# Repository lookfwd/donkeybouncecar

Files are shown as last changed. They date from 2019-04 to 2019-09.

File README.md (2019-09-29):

# Donkey Bounce Car
The Donkey Bounce Car is the [Donkey Car](https://www.donkeycar.com/) + super fancy extra hardware and software.

## Videos

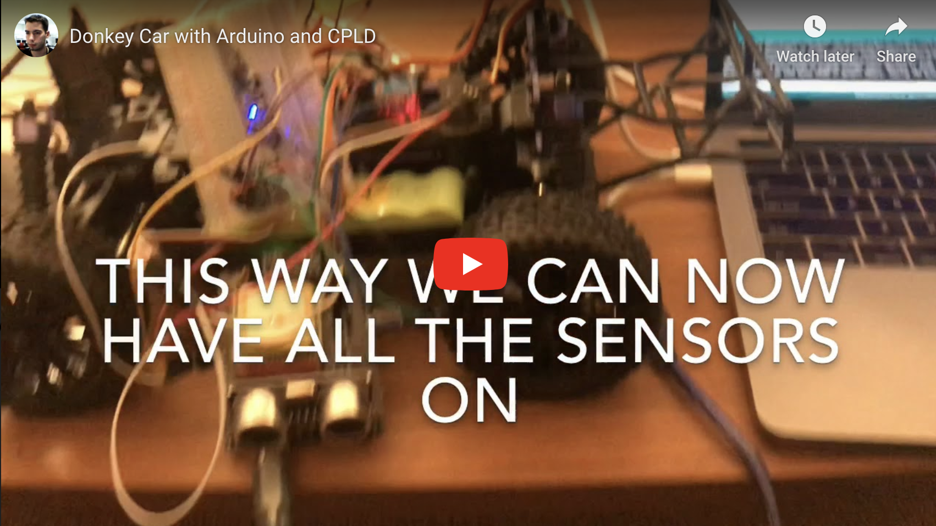
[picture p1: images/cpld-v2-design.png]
Watch the video (https://www.youtube.com/watch?v=cjI4cC8FCgs)


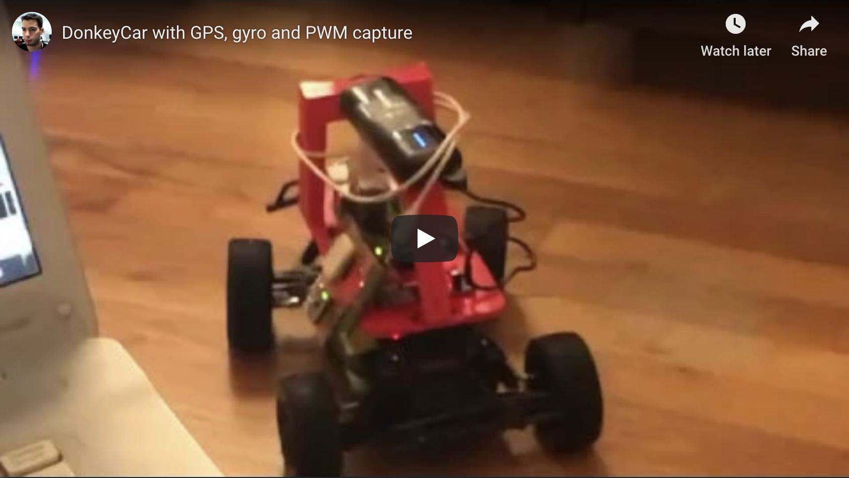
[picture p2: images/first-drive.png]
Watch the video (https://www.youtube.com/watch?v=y7wChCVcuVY)


## Donkey Bounce Shield II

### Goal
The second version of the Donkey Bounce Shield, uses a CPLD to accuratelly measure Servo signals from the Remote Control (RC). It creates PWM signals that drive both steering and throttle and by default it mirrors the signals of the RC. Alternatively, Arduino's serial port can override RC settings and drive the car. It also now supports various types of GPSs and both 6-axis and 9-axis absolute position sensors.

* You can find the PCB [here](https://oshpark.com/shared_projects/81d3538F).
* You can find the CPLD design and JTAG files [here](shield/servo-reader-xc2c64a).
* You can find the latest Arduino Sketch [here](shield/gps-gyro-pwm-sketch).
* You can find the updated ServoTimer1 library [here](shield/ServoTimer1).

The schematic

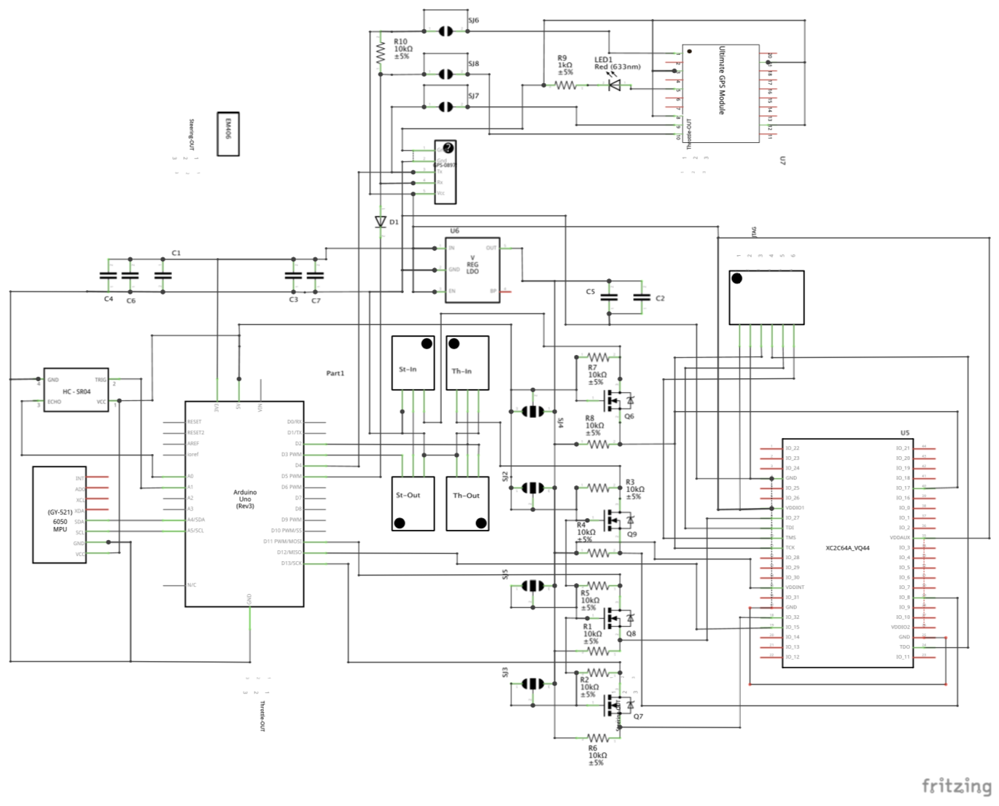
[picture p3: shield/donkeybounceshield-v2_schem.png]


or - 

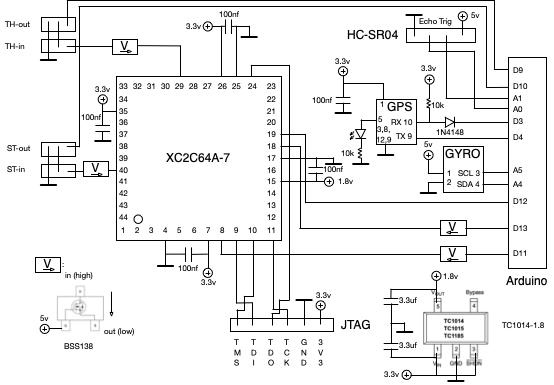
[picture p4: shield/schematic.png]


The Shield

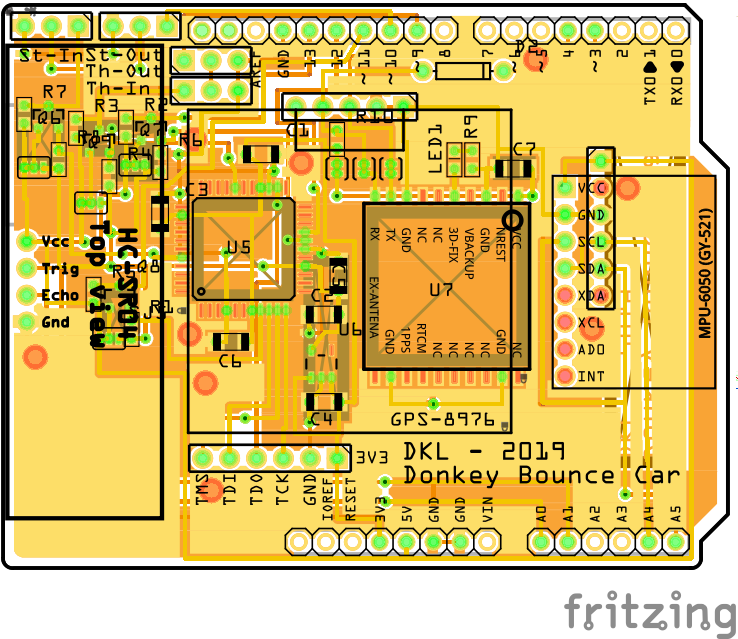
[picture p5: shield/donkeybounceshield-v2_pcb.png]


### Rationale

As soon as I started using the first version of the Donkey Bounce Shield, several limitations became aparent:

1. Servo pulse width measurements were highly inaccurate. Even after using interrupts and other techniques the accuracy was bad.
2. I would have to manually unplug the Remote Control signals in order to create control signals from Arduino.
3. When, after several modifications I was able to have arduino as man-in-the-middle, between the RC and the motors, Donkey Car was making flaky small moves as inaccurate measurements where propagated to the PWM controller.

The reason for inaccurate measurements was the sensitivity on interrupts. More specifically the `cli` command stops interrupts and it's used very often. For example, it's used by the `micros()` Arduino command and it's also very heavily used by the SoftwareSerial module. We need that module in order to read GPS signals.

Bottom line; In order to accurately read PWM signals you need to measure latencies with microsecond-level precision and an Arduino can't do that when it's as busy as it is in our case. I offloaded this work to [custom hardware and more specifically an XC2C64A Xilinx CPLD](servo-reader-xc2c64a).

### References

* [Use the Matrix Glitcher as a Coolrunner II XC2C64A development board](http://blog.dimitrioskouzisloukas.com/2019/08/use-matrix-glitcher-as-coolrunner-ii.html)
* [XC2C64A CoolRunner-II CPLD Datasheet](https://www.xilinx.com/support/documentation/data_sheets/ds311.pdf)
* [Datasheet of GPS smart antenna module, LS20030~3](https://cdn.sparkfun.com/datasheets/GPS/LS20030~3_datasheet_v1.3.pdf)
* [FGPMMOPA6H GPS Standalone Module Data Sheet](https://cdn-shop.adafruit.com/datasheets/GlobalTop-FGPMMOPA6H-Datasheet-V0A.pdf)
* [Adafruit Ultimate GPS v3 Schematic](https://learn.adafruit.com/adafruit-ultimate-gps/downloads)
* [Dangerous Prototypes XC2C64A cpld breakout Schematic](http://dangerousprototypes.com/docs/File:Cct-XC2C_64a-cpld-breakout-v1a.png)
* [TC1014/TC1015/TC1185 Voltage Regulators](http://ww1.microchip.com/downloads/en/devicedoc/21335e.pdf)
* [Logic Level Bidirectional Adaptor Schematic](https://cdn.sparkfun.com/datasheets/BreakoutBoards/Logic_Level_Bidirectional.pdf)
* [5V Tolerance Techniques for CoolRunner-II Devices](https://www.xilinx.com/support/documentation/application_notes/xapp429.pdf)
* [BSS138 N-Channel Logic Level Enhancement Mode Field Effect Transistor](https://cdn.sparkfun.com/datasheets/BreakoutBoards/BSS138.pdf)
* [Adafruit BNO055 Absolute Orientation Sensor](https://learn.adafruit.com/adafruit-bno055-absolute-orientation-sensor?view=all)

## Donkey Bounce Shield I

### What

A shield that adds a GPS, a gyro, PWM monitors and a distance sensor

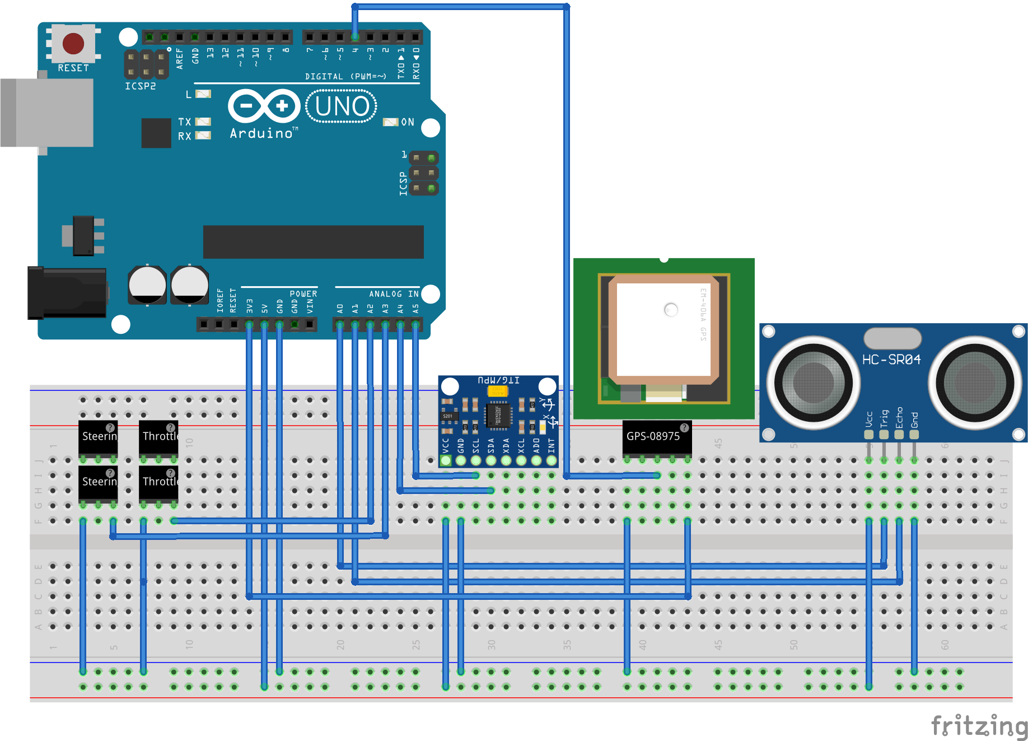
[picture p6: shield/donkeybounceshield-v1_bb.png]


The schematic

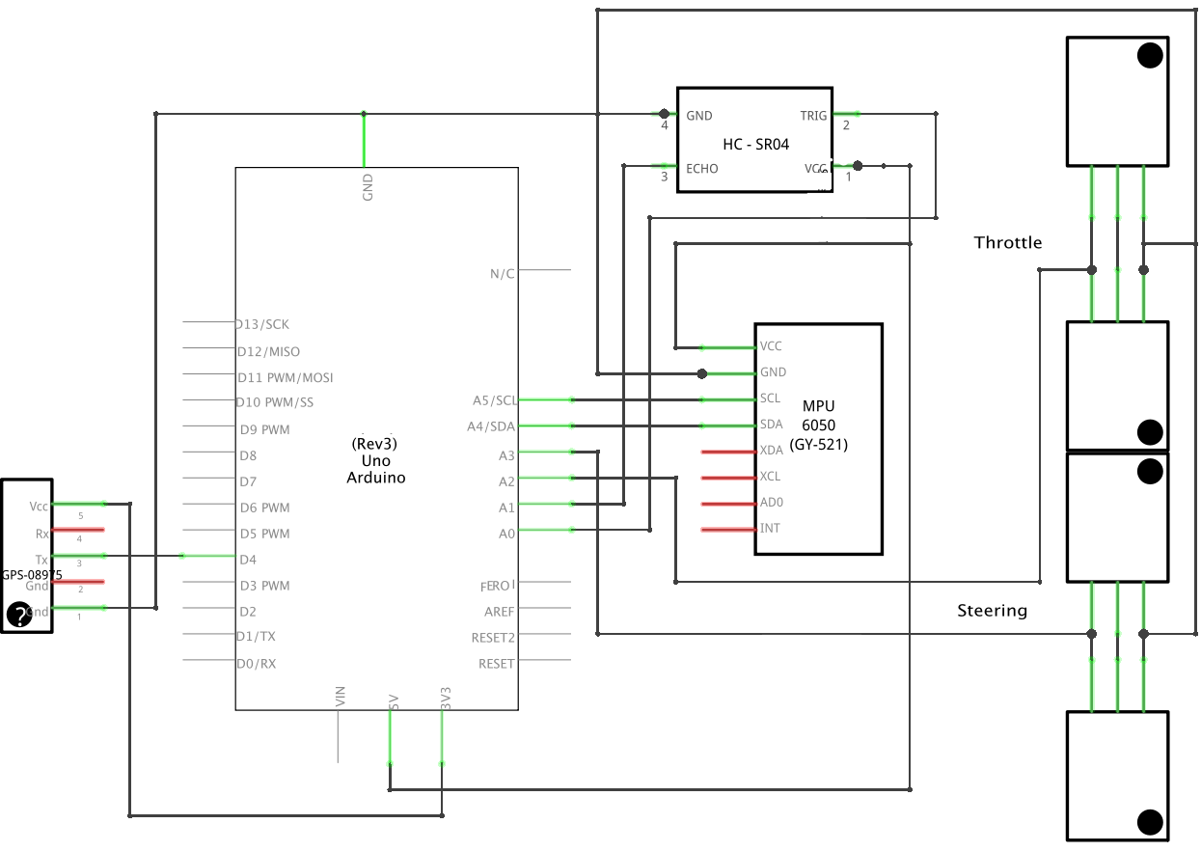
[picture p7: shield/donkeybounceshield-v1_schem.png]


The Shield

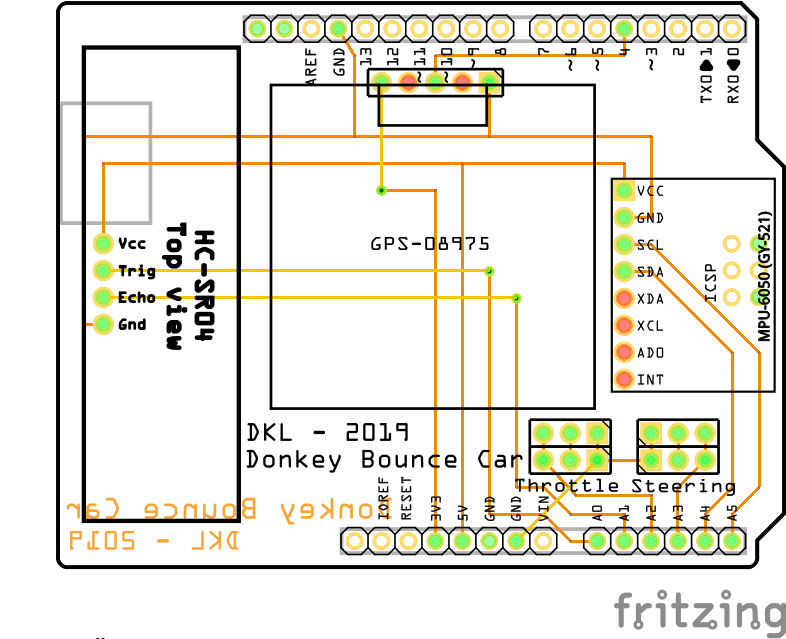
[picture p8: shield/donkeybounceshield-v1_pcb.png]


You can find details about the PCB [here](https://oshpark.com/shared_projects/IXQhfZmE).

### How to

```
ssh pi@192.168.1.124
```

If it's on `Ellipsis Jetpack 15BF`:

```
ssh pi@192.168.1.11
```

Wifi notes: Setting WiFi up via the command line
https://www.raspberrypi.org/documentation/configuration/wireless/wireless-cli.md

Ellipsis Jetpack 15BF

```
$ python a.py
```

This was a good attempt - but didn't work:

```
./usbrawserial /dev/ttyACM0
```

[Ref](http://docs.donkeycar.com/guide/get_driving/):
```
$ cd ~/mycar/
$ python manage.py drive
```

http://192.168.1.124:8887
http://192.168.1.11:8887

### GPS

* GPS Receiver - LS20031 5Hz ([1](https://www.sparkfun.com/products/8975), [2](https://learn.sparkfun.com/tutorials/ls20031-5hz-66-channel-gps-receiver-hookup-guide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), [3](https://cdn.sparkfun.com/datasheets/GPS/LS20030~3_datasheet_v1.3.pdf))

### References

* [Pulse Width Modulation](https://learn.sparkfun.com/tutorials/pulse-width-modulation/all)
* [Arduino Uno SMD](https://www.Uno.cc/en/Main/ArduinoBoardUnoSMD)
* [SPI library](https://www.arduino.cc/en/reference/SPI)
* [Three Ways To Read A PWM Signal With Arduino](http://www.benripley.com/diy/arduino/three-ways-to-read-a-pwm-signal-with-arduino/)
* [MPU-6000 and MPU-6050 Register Map and Descriptions](https://www.invensense.com/wp-content/uploads/2015/02/MPU-6000-Register-Map1.pdf)
* [MPU-6000 and MPU-6050 Product Specification](https://store.invensense.com/datasheets/invensense/MPU-6050_DataSheet_V3%204.pdf)
* [MPU-6050 Accelerometer + Gyro](https://playground.arduino.cc/Main/MPU-6050/#short)
* [USB-ISS  Multifunction USB Communications Module - I2C Mode](https://www.robot-electronics.co.uk/htm/usb_iss_i2c_tech.htm)
* [USB-ISS  Multifunction USB Communications Module - I/O Mode](https://www.robot-electronics.co.uk/htm/usb_iss_io_tech.htm)
* [How to use the accelerometer- gyroscope GY-521](https://create.arduino.cc/projecthub/Nicholas_N/how-to-use-the-accelerometer-gyroscope-gy-521-6dfc19)
* [SparkFun FTDI Basic Breakout - 3.3V](https://www.sparkfun.com/products/9873)
* [pyserial/serial/serialposix.py](https://github.com/pyserial/pyserial/blob/master/serial/serialposix.py)
* [Make Raspberry Pi and Arduino Work as One Team](https://www.sunfounder.com/blog/rpi-ard/)
* [Interface a Raspberry Pi with an Arduino so the two boards can communicate with one another](https://maker.pro/raspberry-pi/tutorial/how-to-connect-and-interface-raspberry-pi-with-arduino)
* [TinyGPSPlus/examples/DeviceExample/DeviceExample.ino](https://github.com/mikalhart/TinyGPSPlus/blob/master/examples/DeviceExample/DeviceExample.ino)
* [LS20031 5Hz (66 Channel) GPS Receiver Hookup Guide](https://learn.sparkfun.com/tutorials/ls20031-5hz-66-channel-gps-receiver-hookup-guide/all)

## Todo

Create a UI using [1](https://sketchfab.com/3d-models/red-dragon-ac2edeb01b9a4d4796c4d34f5d8aa1f2), [2](https://learn.adafruit.com/bno055-absolute-orientation-sensor-with-raspberry-pi-and-beaglebone-black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), [3](https://learn.adafruit.com/assets/24667).

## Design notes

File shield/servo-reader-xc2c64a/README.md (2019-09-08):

# Servo Reader for XC2C64A-CP56

This is a Verilog design using Xilinx ISE WebPACK. 

## Principles of operation

* Arduino controls the "clock" input of the CPLD. Most of the time it runs in 1MHz, allowing the CPLD to measure Servo signals with microsecond accuracy.
* Servo control pulses get generated 50 times a second.
* 25 times per second the Arduino stops the clock and turns the 'scan enable' input to true. Then it scans out the contents of all registers in the CPLD.

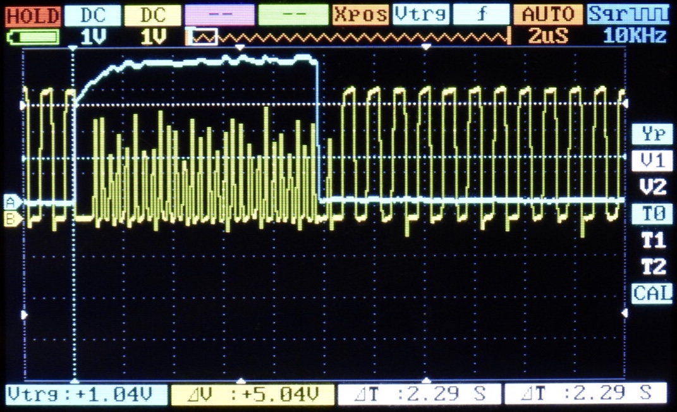
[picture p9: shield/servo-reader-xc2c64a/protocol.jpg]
Basic Protocl


* The fact that measurments take place 25 times per second, means that it's guaranteed that each of the two channels has measured one pulse, since they're created 50 times per second.
* CPLD's registers contain for each of the two channels: a) the 12-bit value of the pulse width measurment (from 0 to 4095 microseconds) b) a two-bit status value which can be in one of the following states: WAIT (Error state - Didn't receive a pulse), RUNNING (Error state - Still measuring), DONE (Success - the 12-bit value is valid), OVERFLOW (Error state - the pulse width was larger than 4095 microseconds).

The CPLD design is very compact. Obviously we need no less than 14 bits per channel, and we use two extra registers for input metastability prevention and edge detection. At the end it's 16 registers per channel. Half of the CPLD is used. It is possible to fit twice as many channels on the same CPLD.

In this folder you will find the following:

## Design

* [servocount1.v](servocount1.v) - Single PWM reader
* [servocount.v](servocount.v) - Top-Level two-channel PWM reader

## Verification

* [servocount_tb.v](servocount_tb.v) - Testbench
* [wave.do](wave.do) - ModelSim simulation layout

## Constraints

* [servocount-cp56.ucf](servocount-cp56.ucf) Constraints for XC2C64A-CP56. It won't work for other package types for the same CPLD

## JTAG files

* [servocount-cp56.jed](servocount-cp56.jed) - JEDEC file for package CP56
* [servocount-cp56.xsvf](servocount-cp56.xsvf) - Scan file for package CP56

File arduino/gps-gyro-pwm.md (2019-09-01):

# Donkeycar

## Todo

https://sketchfab.com/3d-models/red-dragon-ac2edeb01b9a4d4796c4d34f5d8aa1f2

https://learn.adafruit.com/bno055-absolute-orientation-sensor-with-raspberry-pi-and-beaglebone-black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

https://learn.adafruit.com/assets/24667

https://github.com/lookfwd/donkeybouncecar

## Video

Watch the video (https://www.youtube.com/watch?v=y7wChCVcuVY)

## What

A shield that adds a GPS, a gyro, PWM monitors and a distance sensor



The schematic



The Shield



You can find details about the PCB [here](https://oshpark.com/shared_projects/IXQhfZmE).

## How to

```
ssh pi@192.168.1.124
```

If it's on `Ellipsis Jetpack 15BF`:

```
ssh pi@192.168.1.11
```

Wifi notes: Setting WiFi up via the command line
https://www.raspberrypi.org/documentation/configuration/wireless/wireless-cli.md

Ellipsis Jetpack 15BF

```
$ python a.py
```

This was a good attempt - but didn't work:

```
./usbrawserial /dev/ttyACM0
```

[Ref](http://docs.donkeycar.com/guide/get_driving/):
```
$ cd ~/mycar/
$ python manage.py drive
```

http://192.168.1.124:8887
http://192.168.1.11:8887

## GPS

* GPS Receiver - LS20031 5Hz ([1](https://www.sparkfun.com/products/8975), [2](https://learn.sparkfun.com/tutorials/ls20031-5hz-66-channel-gps-receiver-hookup-guide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), [3](https://cdn.sparkfun.com/datasheets/GPS/LS20030~3_datasheet_v1.3.pdf))

## References

* [Pulse Width Modulation](https://learn.sparkfun.com/tutorials/pulse-width-modulation/all)
* [Arduino Uno SMD](https://www.arduino.cc/en/Main/ArduinoBoardUnoSMD)
* [SPI library](https://www.arduino.cc/en/reference/SPI)
* [Three Ways To Read A PWM Signal With Arduino](http://www.benripley.com/diy/arduino/three-ways-to-read-a-pwm-signal-with-arduino/)
* [MPU-6000 and MPU-6050 Register Map and Descriptions](https://www.invensense.com/wp-content/uploads/2015/02/MPU-6000-Register-Map1.pdf)
* [MPU-6000 and MPU-6050 Product Specification](https://store.invensense.com/datasheets/invensense/MPU-6050_DataSheet_V3%204.pdf)
* [MPU-6050 Accelerometer + Gyro](https://playground.arduino.cc/Main/MPU-6050/#short)
* [USB-ISS  Multifunction USB Communications Module - I2C Mode](https://www.robot-electronics.co.uk/htm/usb_iss_i2c_tech.htm)
* [USB-ISS  Multifunction USB Communications Module - I/O Mode](https://www.robot-electronics.co.uk/htm/usb_iss_io_tech.htm)
* [How to use the accelerometer- gyroscope GY-521](https://create.arduino.cc/projecthub/Nicholas_N/how-to-use-the-accelerometer-gyroscope-gy-521-6dfc19)
* [SparkFun FTDI Basic Breakout - 3.3V](https://www.sparkfun.com/products/9873)
* [pyserial/serial/serialposix.py](https://github.com/pyserial/pyserial/blob/master/serial/serialposix.py)
* [Make Raspberry Pi and Arduino Work as One Team](https://www.sunfounder.com/blog/rpi-ard/)
* [Interface a Raspberry Pi with an Arduino so the two boards can communicate with one another](https://maker.pro/raspberry-pi/tutorial/how-to-connect-and-interface-raspberry-pi-with-arduino)
* [TinyGPSPlus/examples/DeviceExample/DeviceExample.ino](https://github.com/mikalhart/TinyGPSPlus/blob/master/examples/DeviceExample/DeviceExample.ino)
* [LS20031 5Hz (66 Channel) GPS Receiver Hookup Guide](https://learn.sparkfun.com/tutorials/ls20031-5hz-66-channel-gps-receiver-hookup-guide/all)

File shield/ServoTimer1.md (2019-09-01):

# ServoTimer1

ServoTimer1 from https://playground.arduino.cc/ComponentLib/Servotimer1/

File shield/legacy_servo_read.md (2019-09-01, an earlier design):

# Old routine for reading PWM

```
#define SERVO_RESET 1500

class Channel {
  volatile bool lastState;
  volatile long lastLowToHigh;
  volatile int timeUs;
  volatile int lastValue;

public:
  Channel()
    : lastState(false)
    , lastLowToHigh(0)
    , timeUs(SERVO_RESET)
    , lastValue(SERVO_RESET)
  {
  }

  bool onChange(bool state)
  {
    if (state == lastState) {
      return false;
    }
    lastState = state;

    unsigned long now = micros();
    if (state) {
      // 0->1: Capture frame start
      lastLowToHigh = now;
      return;
    }

    // 1->0: Capture time
    timeUs = (now - lastLowToHigh);

    if (lastValue != timeUs) {
      lastValue = timeUs;
      return true;
    }
    return false;
  }

  int getTimeUs() {
    return timeUs;
  }
};

Channel d2throttle, d3steering;

uint8_t d2_mask, d3_mask;
volatile uint8_t *interruptPort;

void pinx_ISR() {
  // Way faster than digitalRead(). digitalRead() might cost 5us, which is bad
  // because it adds tons of jitter and we had to do it twice, once for each
  // pin.
  // https://forum.arduino.cc/index.php?topic=337578.msg2327508#msg2327508
  uint8_t portv = *interruptPort;
  if (d2throttle.onChange(portv & d2_mask)) {
    servo1.writeDirect(d2throttle.getTimeUs());
  }
  if (d3steering.onChange(portv & d3_mask)) {
    // Drunk mode:
    //  + int(100.0 * sin((micros() % 6000000)/1000000.))
    servo2.writeDirect(d3steering.getTimeUs());
  }
}

setup() {
  interruptPort = portInputRegister(digitalPinToPort(2));
  d2_mask = digitalPinToBitMask(2);
  d3_mask = digitalPinToBitMask(3);
  if (interruptPort != portInputRegister(digitalPinToPort(3)))
  {
    Serial.println("Ooops, Interrupt pins not in the same port");
    while(1);
  }

  // PWM Read
  pinMode(2, INPUT);
  pinMode(3, INPUT);
  attachInterrupt(digitalPinToInterrupt(2), pinx_ISR, CHANGE);
  attachInterrupt(digitalPinToInterrupt(3), pinx_ISR, CHANGE);
}

```

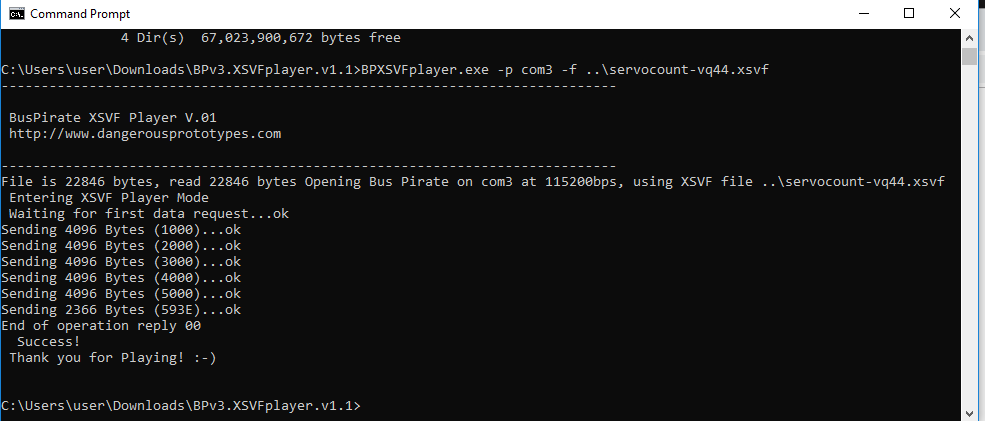
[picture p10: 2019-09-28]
images/xsvfplayer.png

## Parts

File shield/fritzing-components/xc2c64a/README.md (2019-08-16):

# Make fritzing model

Based on `DSPIC30f4011` which also has package of tqfp44. I didn't have to change the pcb nor breadboard. I re-did the XML (`.fzp` file - using `make-fzp.py`) because it was messed up and also had to do serious modifications to `xc2c64a-schematic.svg` (using `make-schematic.py`) because OmniGraffle was creating very different `.svg` than expected and wasted my time.

Overall I followed the process described [here](https://www.deviceplus.com/how-tos/creating-custom-parts-fritzing/4/) and used as resources the [xilinx vq44 package spec](https://www.xilinx.com/support/documentation/package_specs/vq44.pdf), the [CoolRunner-II CPLD breakout board description page](http://dangerousprototypes.com/docs/CoolRunner-II_CPLD_breakout_board) and [shematic](http://dangerousprototypes.com/docs/images/e/e8/Cct-XC2C_64a-cpld-breakout-v1a.png), the [XC2C64A CoolRunner-II CPLD datasheet](https://www.xilinx.com/support/documentation/data_sheets/ds311.pdf), and the [seeedstudio page for the dev board](https://www.seeedstudio.com/XC2C64A-CoolRunner-II-CPLD-development-board-p-800.html).

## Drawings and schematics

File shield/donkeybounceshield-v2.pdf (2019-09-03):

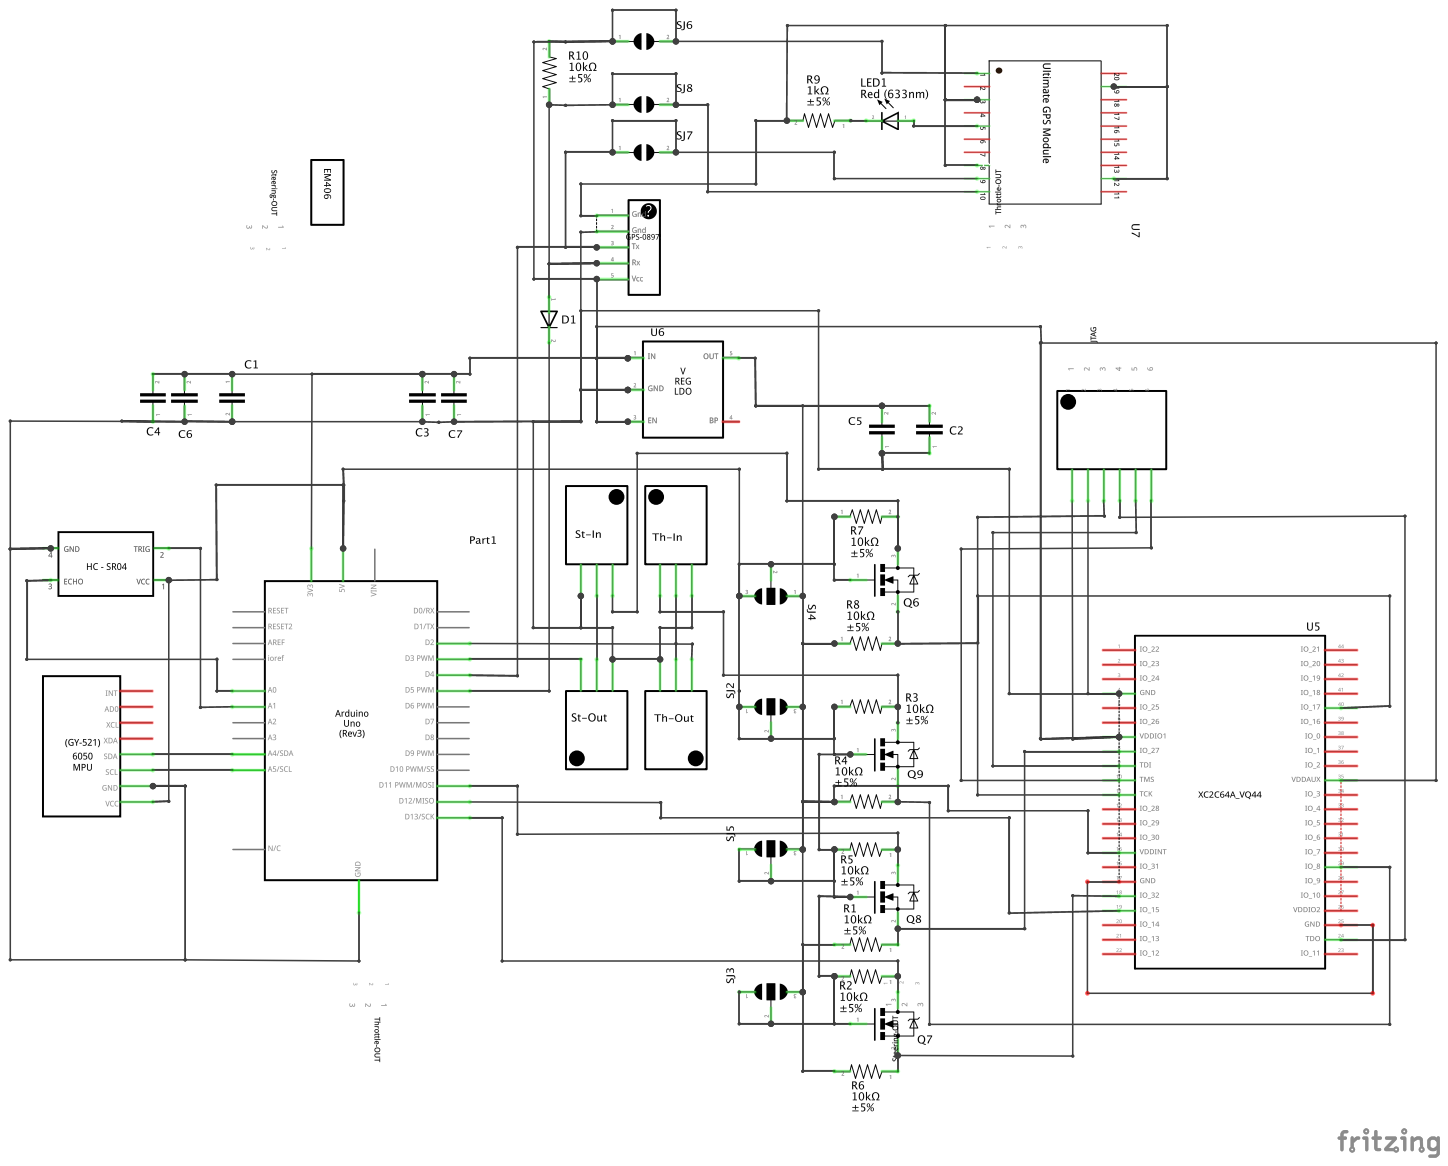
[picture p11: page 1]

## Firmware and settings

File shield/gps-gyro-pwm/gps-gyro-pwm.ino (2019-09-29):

// TODO:
// - Make sure CPLDs are with weak high-impedence
// - Make sure you tie all I/O to the ground
// - Make sure PCB has all ground on the lower layer
// - Add optional resistors to PCB
// - Add the 3 alternative GPS solutions
// - Prototype both power supply and bare-n-mosfet Volt adapters
// - Add JTAG pins to PCB
// - Make sure I export/save the GPS component

#define ENABLE_GYRO
#define ENABLE_GYRO2
#define ENABLE_GPS
#define ENABLE_SONAR
#define ENABLE_PWM

#ifdef ENABLE_SONAR
#include <NewPing.h>
NewPing sonar(A1, A0);
#endif  // ENABLE_SONAR

#ifdef ENABLE_GYRO2
#include <Wire.h>
#endif  // ENABLE_GYRO2

#define SERVO_RESET 1500


//---------------------------------------------------------------------

#ifdef ENABLE_PWM
struct ServoValue
{
  char status;
  uint16_t timeUs;
};

class ServoReader
{
    const int PIN_CLK = 11;
    const int PIN_SCAN_EN = 13;
    const int PIN_SCAN_IN = 12;
    const char *STATES = "WRDO";  // Wait, Running, Done, Overflow

    static void clkStart()
    {
      // PCINT3/OC2A/MOSI <-> PB3 <-> Arduino Pin 11
      TCCR2A = TCCR2A & ~_BV(COM2A1) | _BV(COM2A0);
    }

    static void clkStop()
    {
      // PCINT3/OC2A/MOSI <-> PB3 <-> Arduino Pin 11
      TCCR2A = TCCR2A & ~_BV(COM2A1) & ~_BV(COM2A0);
    }

    static void clkLow()
    {
      asm("cbi %0, %1 \n"
          : : "I" (_SFR_IO_ADDR(PORTB)), "I" (PORTB3)
         );
    }

    static void tick()
    {
      asm("sbi %0, %1 \n"
          "cbi %0, %1 \n"

          : : "I" (_SFR_IO_ADDR(PORTB)), "I" (PORTB3)
         );
    }

    static void scanHigh()
    {
      asm("sbi %0, %1 \n"
          : : "I" (_SFR_IO_ADDR(PORTB)), "I" (PORTB5)
         );
    }

    static void scanLow()
    {
      asm("cbi %0, %1 \n"
          : : "I" (_SFR_IO_ADDR(PORTB)), "I" (PORTB5)
         );
    }

  public:

    void init()
    {
      if (digitalPinToPort(PIN_CLK) != 2) {
        Serial.println("Expected clock to be in PORTB");
        while (1);
      }
      if (digitalPinToPort(PIN_SCAN_IN) != 2) {
        Serial.println("Expected scan_out to be in PORTB");
        while (1);
      }
      if (digitalPinToPort(PIN_SCAN_EN) != 2) {
        Serial.println("Expected scan_en to be in PORTB");
        while (1);
      }
      if (digitalPinToBitMask(PIN_CLK) != 8) {
        Serial.println("Expected mask(clock) to be 8");
        while (1);
      }
      if (digitalPinToBitMask(PIN_SCAN_IN) != 16) {
        Serial.println("Expected mask(scan_out) to be 16");
        while (1);
      }
      if (digitalPinToBitMask(PIN_SCAN_EN) != 32) {
        Serial.println("Expected mask(scan_en) to be 16");
        while (1);
      }

      OCR2A = 0x00; // This gives 1MHz given prescaler of 8
      TCCR2A = _BV(WGM21) | ~_BV(WGM20); //  compare output mode bits to toggle mode (COM2A1:0 = 1)
      TCCR2B = _BV(CS21); // Prescaler clk/8

      clkLow();

      pinMode(PIN_CLK, OUTPUT);
      pinMode(PIN_SCAN_EN, OUTPUT);
      pinMode(PIN_SCAN_IN, INPUT);

      ServoValue sv[2];
      read(sv);  // At the end of read(), clock is (re)started
    }

    void read(ServoValue *sv)
    {
      // 0. See "Arduino Inline Assembly" book
      // 1. See also here: https://www.arduino.cc/en/Reference/PortManipulation
      // 2. $ export PATH=$PATH:/Applications/Arduino.app/Contents/Java/hardware/tools/avr/bin/
      // 3. avr-objdump -S /var/folders/p7/xkm56c997zj9cj4rpx35rc2r0000gn/T/arduino_build_705153/read-servo-cpld.ino.elf > read-servo-cpld.txt

      uint8_t s0h = 0, s0l = 0;
      uint8_t s1h = 0, s1l = 0;

      clkLow(); // Stop the clock and start the scan
      clkStop();
      scanHigh();

      uint8_t oldSREG = SREG;  // Clear interrupts. Stop the world!
      cli();

      uint8_t tmp = PORTB;
      uint8_t bset = tmp | (1 << PORTB3);
      uint8_t bclear = tmp & ~(1 << PORTB3);

#define readDigit(r) __asm__ __volatile__ (  \
    "add %0, %0  \n"                           \
    "sbic %1, %2 \n"                           \
    "ori %0, 1 \n"                             \
    "out %3, %4  \n"                           \
    "out %3, %5  \n"                           \
    : "+r" (r)                                 \
    : "I" (_SFR_IO_ADDR(PINB)), "I" (PINB4),   \
    "I" (_SFR_IO_ADDR(PORTB)),               \
    "r" (bset), "r" (bclear)                 \
                                          );

      readDigit(s0h);
      readDigit(s0h);
      readDigit(s0h);
      readDigit(s0h);
      readDigit(s0h);
      readDigit(s0h);

      readDigit(s0l);
      readDigit(s0l);
      readDigit(s0l);
      readDigit(s0l);
      readDigit(s0l);
      readDigit(s0l);
      readDigit(s0l);
      readDigit(s0l);

      readDigit(s1h);
      readDigit(s1h);
      readDigit(s1h);
      readDigit(s1h);
      readDigit(s1h);
      readDigit(s1h);

      readDigit(s1l);
      readDigit(s1l);
      readDigit(s1l);
      readDigit(s1l);
      readDigit(s1l);
      readDigit(s1l);
      readDigit(s1l);
      readDigit(s1l);

      SREG = oldSREG;  // 9.5us later, we're done! Restore.
      // (28 x 5 clocks per loop + extras) / 16MHz

      scanLow();
      clkStart();

      sv[0].status = STATES[s0h >> 4];
      sv[0].timeUs = ((s0h & 0xf) << 8) + s0l;
      sv[1].status = STATES[s1h >> 4];
      sv[1].timeUs = ((s1h & 0xf) << 8) + s1l;
    }
};

ServoReader sr;

#include <ServoTimer1.h>
ServoTimer1 servo1, servo2;

#endif  // ENABLE_PWM

//---------------------------------------------------------------------


#ifdef ENABLE_GYRO

#include <Adafruit_BNO055.h>
Adafruit_BNO055 bno = Adafruit_BNO055(55, BNO055_ADDRESS_B);
#endif  // ENABLE_GYRO


//---------------------------------------------------------------------


#define BUFSIZE 200
class LineProcessor
{
    typedef void (*CallbackT)(const char* line);
    char buf[BUFSIZE];
    int cnt;
    bool waitForNewline;
    CallbackT callback;

  public:

    LineProcessor(CallbackT callback_)
      : cnt(0)
      , waitForNewline(true)
      , callback(callback_)
    {
      buf[cnt] = 0;
    }

    void addChar(uint8_t c) {
      if (cnt == BUFSIZE) {
        waitForNewline = true;
      }
      //CR and LF are control characters, respectively coded 0x0D (13 decimal) and 0x0A
      if (c == '\r' || c == '\n') {
        if ((!waitForNewline) && (cnt > 0)) {
          buf[cnt] = 0;
          callback(buf);
        }
        cnt = buf[0] = 0;
        waitForNewline = false;
      }
      else if (!waitForNewline) {
        buf[cnt] = c;
        ++cnt;
      }
    }
};


//---------------------------------------------------------------------


#ifdef ENABLE_GPS

#include <SoftwareSerial.h>
static const int RXPin = 4, TXPin = 3;
SoftwareSerial ss(RXPin, TXPin);

unsigned long lastGpggaTime = millis();
void gpsLineDone(const char* line)
{
  // http://aprs.gids.nl/nmea/#gga
  // Example: "4043.4476,N,07359.6348,W,1,6"
  //eg2. $--GGA,hhmmss.ss,llll.ll,a,yyyyy.yy,a,x,xx,x.x,x.x,M,x.x,M,x.x,xxxx
  //
  //hhmmss.ss = UTC of position
  //llll.ll = latitude of position
  //a = N or S
  //yyyyy.yy = Longitude of position
  //a = E or W
  //x = GPS Quality indicator (0=no fix, 1=GPS fix, 2=Dif. GPS fix)
  //xx = number of satellites in use
  //x.x = horizontal dilution of precision
  //x.x = Antenna altitude above mean-sea-level
  //M = units of antenna altitude, meters
  //x.x = Geoidal separation
  //M = units of geoidal separation, meters
  //x.x = Age of Differential GPS data (seconds)
  //xxxx = Differential reference station ID

  if (strncmp("$GPGGA,", line, 7)) {
    return;
  }
  // Don't forget to check the checksum on GPS logs.
  Serial.print("G ");
  Serial.print(line);
  Serial.print(" ");
  unsigned long now = millis();
  Serial.println(now - lastGpggaTime);
  lastGpggaTime = now;
}

LineProcessor np(gpsLineDone);

#endif  // ENABLE_GPS


// Anything more frequent than 14 updates/second will
// keep this under control. No data for more than 70 ms
// will revert to the remote control.
#define MILLISECOND_OVERRIDE 70

unsigned long lastSOverride = 0;
unsigned long lastTOverride = 0;
void consoleLineDone(const char* line)
{
  if (strncmp("S ", line, 2) == 0) {
    servo2.writeDirect(atoi(line + 2));
    lastSOverride = millis();
  }
  else if (strncmp("T ", line, 2) == 0) {
    servo1.writeDirect(atoi(line + 2));
    lastTOverride = millis();
  }
}

LineProcessor mp(consoleLineDone);


//---------------------------------------------------------------------

unsigned long lastGyroMeasure = micros();
unsigned long lastServoMeasure = micros();
unsigned long lastSonarMeasure = micros();

const int MPU = 0x68;

void setup() {

  // Init Serial
  Serial.begin(115200);
  while (!Serial) {
    ; // wait for serial port to connect. Needed for Native USB only
  }

  //---------------------------------------------------------------------

#ifdef ENABLE_GYRO2
  Wire.begin();
  Wire.beginTransmission(MPU);
  Wire.write(0x6B);
  Wire.write(0);
  Wire.endTransmission(true);
#endif  // ENABLE_GYRO2

  //---------------------------------------------------------------------

#ifdef ENABLE_PWM
  sr.init();
  servo1.attach(9);
  servo2.attach(10);
#endif  // ENABLE_PWM

  //---------------------------------------------------------------------

#ifdef ENABLE_GYRO
  // Init Gyro
  if (!bno.begin())
  {
    /* There was a problem detecting the BNO055 ... check your connections */
    Serial.println("Ooops, no BNO055 detected ... Check your wiring or I2C ADDR!");
    while (1);
  }

  delay(100);

  bno.setExtCrystalUse(true);
#endif  // ENABLE_GYRO


  //---------------------------------------------------------------------


  // GPS serial
#ifdef ENABLE_GPS
  ss.begin(57600);
#endif  // ENABLE_GPS
}

void loop()
{
#ifdef ENABLE_GPS
  while (ss.available() > 0) {
    np.addChar(ss.read());  // A Seria.print() might happen in here.
  }
#endif  // ENABLE_GPS

  while (Serial.available() > 0) {
    mp.addChar(Serial.read());
  }

  unsigned long now = micros();


  //---------------------------------------------------------------------


#if defined ENABLE_GYRO || defined ENABLE_GYRO2
  if ((now - lastGyroMeasure) > 500000) { // 2Hz

    Serial.print("A ");

#ifdef ENABLE_GYRO
    // Possible vector values can be:
    // - VECTOR_ACCELEROMETER - m/s^2
    // - VECTOR_MAGNETOMETER  - uT
    // - VECTOR_GYROSCOPE     - rad/s
    // - VECTOR_EULER         - degrees
    // - VECTOR_LINEARACCEL   - m/s^2
    // - VECTOR_GRAVITY       - m/s^2
    sensors_event_t orientation, acceleration;
    bno.getEvent(&orientation);
    // Acceleration - gravity:
    bno.getEvent(&acceleration, Adafruit_BNO055::VECTOR_LINEARACCEL);

    Serial.print(orientation.orientation.x, 2);
    Serial.print(' ');
    Serial.print(orientation.orientation.y, 2);
    Serial.print(' ');
    Serial.print(orientation.orientation.z, 2);
    Serial.print(' ');
    Serial.print(acceleration.acceleration.x, 2);
    Serial.print(' ');
    Serial.print(acceleration.acceleration.y, 2);
    Serial.print(' ');
    Serial.print(acceleration.acceleration.z, 2);
#endif  // ENABLE_GYRO

#if defined ENABLE_GYRO && defined ENABLE_GYRO2
    Serial.print(' ');
#endif  // defined ENABLE_GYRO && defined ENABLE_GYRO2

#ifdef ENABLE_GYRO2
    int16_t AcX, AcY, AcZ, GyX, GyY, GyZ;
    {
      Wire.beginTransmission(MPU);
      Wire.write(0x3B);
      Wire.endTransmission(false);
      Wire.requestFrom(MPU, 14, true);
      AcX = Wire.read() << 8 | Wire.read();
      AcY = Wire.read() << 8 | Wire.read();
      AcZ = Wire.read() << 8 | Wire.read();
      Wire.read();  // Tempeature H
      Wire.read();  // Tempeature L
      GyX = Wire.read() << 8 | Wire.read();
      GyY = Wire.read() << 8 | Wire.read();
      GyZ = Wire.read() << 8 | Wire.read();
    }

    Serial.print(AcX);
    Serial.print(' ');
    Serial.print(AcY);
    Serial.print(' ');
    Serial.print(AcZ);
    Serial.print(' ');
    Serial.print(GyX);
    Serial.print(' ');
    Serial.print(GyY);
    Serial.print(' ');
    Serial.print(GyZ);

#endif  // ENABLE_GYRO2

    Serial.println();

    lastGyroMeasure = now;
  }
#endif  // defined ENABLE_GYRO || defined ENABLE_GYRO2


  //---------------------------------------------------------------------


#ifdef ENABLE_SONAR
  if ((now - lastSonarMeasure ) > 500000) { // 2Hz
    int cm = sonar.ping_cm();
    Serial.print("R ");
    Serial.println(cm);
    lastSonarMeasure = now;
  }
#endif  // ENABLE_SONAR


  //---------------------------------------------------------------------

#ifdef ENABLE_PWM
  if ((now - lastServoMeasure) > 40000) { // 25Hz

    ServoValue sv[2];
    sr.read(sv);

    unsigned long nowMs = now / 1000;

    if (sv[0].status == 'D') {
      if (nowMs > (lastTOverride + MILLISECOND_OVERRIDE)) {
        servo1.writeDirect(sv[0].timeUs);
      }
      Serial.print("T ");
      Serial.println(sv[0].timeUs);
    }
    if (sv[1].status == 'D') {
      if (nowMs > (lastSOverride + MILLISECOND_OVERRIDE)) {
        servo2.writeDirect(sv[1].timeUs
                           // + int(100.0 * sin((now % 6000000)/1000000.))  // Drunk mode:
                          );
      }
      Serial.print("S ");
      Serial.println(sv[1].timeUs);
    }

    lastServoMeasure = now;
  }
#endif  // ENABLE_PWM
}

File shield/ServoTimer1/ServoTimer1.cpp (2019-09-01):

#include <ServoTimer1.h>
#include <avr/interrupt.h>
#include <avr/io.h>

/*
  ServoTimer1.h - Hardware Servo Timer Library
  Author: Jim Studt, jim@federated.com
  Copyright (c) 2007 David A. Mellis.  All right reserved.

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
  You should have received a copy of the GNU Lesser General Public
  License along with this library; if not, write to the Free Software
  Foundation, Inc., 51 Franklin St, Fifth Floor, Boston, MA  02110-1301  USA
*/


uint8_t ServoTimer1::attached9 = 0;
uint8_t ServoTimer1::attached10 = 0;

void ServoTimer1::seizeTimer1()
{
    uint8_t oldSREG = SREG;

    cli();
    TCCR1A = _BV(WGM11); /* Fast PWM, ICR1 is top */
    TCCR1B = _BV(WGM13) | _BV(WGM12) /* Fast PWM, ICR1 is top */
	| _BV(CS11) /* div 8 clock prescaler */
	;
    OCR1A = 3000;
    OCR1B = 3000;
    ICR1 = clockCyclesPerMicrosecond()*(20000L/8);  // 20000 uS is a bit fast for the refresh, 20ms, but 
                                                    // it keeps us from overflowing ICR1 at 20MHz clocks
                                                    // That "/8" at the end is the prescaler.
#if defined(__AVR_ATmega168__) || defined(__AVR_ATmega328P__)
    TIMSK1 &=  ~(_BV(OCIE1A) | _BV(OCIE1B) | _BV(TOIE1) );
#else
    TIMSK &= ~(_BV(TICIE1) | _BV(OCIE1A) | _BV(OCIE1B) | _BV(TOIE1) );
#endif
    SREG = oldSREG;  // undo cli()    
}

void ServoTimer1::releaseTimer1()
{;}


#define NO_ANGLE (0xff)

ServoTimer1::ServoTimer1() : pin(0),angle(NO_ANGLE),min16(34),max16(150)
{}

void ServoTimer1::setMinimumPulse(uint16_t t)
{
    min16 = t/16;
}

void ServoTimer1::setMaximumPulse(uint16_t t)
{
    max16 = t/16;
}

uint8_t ServoTimer1::attach(int pinArg)
{
    if ( pinArg != 9 && pinArg != 10) return 0;

    pin = pinArg;
    angle = NO_ANGLE;
    digitalWrite(pin,0);
    pinMode(pin,OUTPUT);

    if ( !attached9 && !attached10) seizeTimer1();

    // muck with timer flags
    if ( pin == 9) {
	attached9 = 1;
	TCCR1A = TCCR1A & ~_BV(COM1A0) | _BV(COM1A1);
    } else {
	attached10 = 1;
	TCCR1A = TCCR1A & ~_BV(COM1B0) | _BV(COM1B1);
    }
    return 1;
}

void ServoTimer1::detach()
{
    // muck with timer flags
    if ( pin == 9) {
	attached9 = 0;
	TCCR1A = TCCR1A & ~_BV(COM1A0) & ~_BV(COM1A1);
    } else {
	attached10 = 0;
	TCCR1A = TCCR1A & ~_BV(COM1B0) & ~_BV(COM1B1);
    }
    pinMode(pin,INPUT);

    if ( !attached9 && !attached10) releaseTimer1();
}

void ServoTimer1::write(int angleArg)
{
    uint16_t p;

    if ( angleArg < 0) angleArg = 0;
    if ( angleArg > 180) angleArg = 180;
    angle = angleArg;

    // bleh, have to use longs to prevent overflow, could be tricky if always a 16MHz clock, but not true
    // That 8L on the end is the TCNT1 prescaler, it will need to change if the clock's prescaler changes,
    // but then there will likely be an overflow problem, so it will have to be handled by a human.
    p = (min16*16L*clockCyclesPerMicrosecond() + (max16-min16)*(16L*clockCyclesPerMicrosecond())*angle/180L)/8L;
    if ( pin == 9) OCR1A = p;
    else OCR1B = p;
}

void ServoTimer1::writeDirect(int microseconds)
{
    // That 8L on the end is the TCNT1 prescaler, it will need to change if the clock's prescaler changes,
    uint16_t p = microseconds * clockCyclesPerMicrosecond() / 8L;
    if ( pin == 9) OCR1A = p;
    else OCR1B = p;
}

uint8_t ServoTimer1::read()
{
    return angle;
}

uint8_t ServoTimer1::attached()
{
    if ( pin == 9 && attached9) return 1;
    if ( pin == 10 && attached10) return 1;
    return 0;
}

void ServoTimer1::refresh()
{
    ;
}

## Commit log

2019-05-21 add PCB details
2019-08-16 adds component for xiling coolrunner CPLD
    [prototype-xc2c64a.fzz]
2019-09-01 backup old way to read PWM. This was flaky because it was sensitive to disabled interrupts (cli) which happens all the time, including SoftwareSerial and micros()
2019-09-01 Adds fixed ServoTimer1 library
    [ServoTimer1.cpp]
2019-09-03 ready for review
    [donkeybounceshield-old.fzz, donkeybounceshield.fzz]
2019-09-04 more tidy
    [donkeybounceshield.fzz, prototype-xc2c64a.fzz]
2019-09-06 with ground fill
    [donkeybounceshield.fzz]
2019-09-08 New Shield PCB v.2 - https://oshpark.com/shared_projects/81d3538F
    [donkeybounceshield-v1.fzz, donkeybounceshield-v2.fzz, donkeybounceshield.fzz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]
2019-09-08 move fritzing components to arduino
    [prototype-xc2c64a.fzz]
2019-09-08 Adds CPLD Servo Reader design
2019-09-08 file cleanup and restructuring
    [donkeybounceshield-v1.fzz, donkeybounceshield-v2.fzz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]
2019-09-29 works new board
